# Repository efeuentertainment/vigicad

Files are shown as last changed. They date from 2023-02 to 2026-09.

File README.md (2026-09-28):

Hier entsteht die Bauanleitung zum Botkin 2S, der neuesten Version des Botkin Roboters, basierend auf dem Vigibot Minus 2S

# Minus-Type 2S Robot für Botkins

## Inhalt

<details open>
<summary>[Diesen Abschnitt verbergen]</summary>

* [1. Generelle Info](#1-generelle-info)
* [2. Voraussetzungen](#2-voraussetzungen)
* [3. Teileliste](#3-teileliste)
* [4. Minus Type 2S Zusammenbau](#4-minus-type-2S-zusammenbau)
  * [4.1 Software Installieren](#41-software-installieren)
  * [4.2 Vigibot Online Konfiguration](#42-vigibot-online-konfiguration)
  * [4.3 Zusammenbau Motorplatte](#43-zusammenbau-motorplatte)
  * [4.4 Zusammenbau Body](#44-zusammenbau-body)
  * [4.5 Roboter mit dem WLAN verbinden](#45-roboter-mit-dem-wlan-verbinden)
  * [4.6 Zusammenbau Greifer und Kopf](#46-zusammenbau-greifer-und-kopf)
  * [4.7 Finale Fertigstellung](#47-finale-fertigstellung)
  * [4.8 Optionale Schritte](#48-optionale-schritte)
  * [4.9 Funktionstest](#49-funktionstest)
* [5. Troubleshooting](#5-troubleshooting)
* [6. Credits](#6-credits)

</details>

# 1. Generelle Info
* Dieser Leitfaden behandelt den Botkins 2S, erhältlich als Kit von Botkins oder [robot-maker.com](https://www.robot-maker.com/shop/kits-robots/284-kit-minus-2s-284.html)
* Der Einfachheit halber wird hier nur die Kit-Version beschrieben. Werden Teile selber beschafft, müssen einzelne Teile selber aus den gelisteten Teilen zusammengesucht werden.
* Die Angaben zu rechts oder links in dieser Anleitung sind immer in Fahrtrichtung gesehen.

## 1.1 Das Botkins Charity Project
Erfahre mehr über das Botkins Charity Project:

* Botkins ist ein nichtgewinnorientierter (gemeinnütziger) Verein. Die Arbeit des Vereinsteams geschiecht auf freiwilligenbasis ohne finanzielle Kompensation. Maker:innen können einen Obulus erhalten.
* [botkins.ch](https://botkins.ch)&#x20;
* [Hackaday Page](https://hackaday.io/project/180558-botkins-charity-project)

## 1.2 Vigibot
Erfahre mehr über Vigibot:
Das französische Roboter-Projekt, dessen Software und Hardware Design Botkins benutzt.

* [Robot Maker Post](https://www.robot-maker.com/forum/topic/13010-what-is-vigibot-quest-ce-que-vigibot/)
* [Drive a robot Vigibot.com](https://www.vigibot.com/)

Als Basis dient die Standard Vigibot Minus-Type Version 2S (siehe Bild). Botkins ist zusätlich mit einem LTE/4G Stick ausgerüstet.

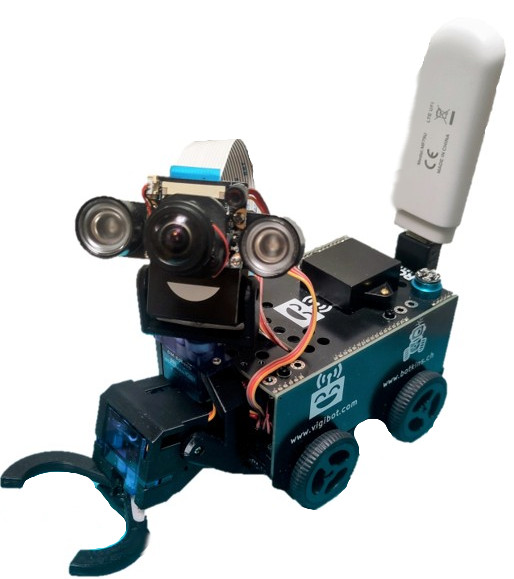
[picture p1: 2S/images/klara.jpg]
Botkins S2


* Wenn du für Botkins einen Roboter bauen möchtest, melde dich bei uns und wir senden dir die nötigen Informationen und den Zugang zu Resourcen.
* Als Maker kannst du die Farbe der 3D-gedruckten Teile selber wählen, sie ist nicht vorgegeben. Kaufst du ein Komplettkit auf robot-maker.com, kannst du dort je nach Verfügbarkeit Teilefarben wählen.
* Der Bau des ersten Roboters kann etwa 5 Stunden dauern, möglicherweise auch länger. Nach etwas Übung dauert der Bau etwa 2 Stunde pro Roboter.
* Bestelle bei uns oder über robot-maker.com das Komplettkit und leg los!

[⬆️ Zurück zum Inhaltsverzeichnis](#inhalt)

# 2. Voraussetzungen

Du benötigst:

* Komplettkit Minus-Type S2 [robot-maker.com](https://www.robot-maker.com/shop/kits-robots/284-kit-minus-2s-284.html) oder bestellbar bei uns an Adresse
* Internetzugang (SIM-Karte mit mobilen Daten, WLAN oder Ethernet-LAN), PC.
* Ein 3D-Drucker ist derzeit nicht erforderlich. Wenn du die 3D-Teile selbst drucken möchtest, werden M2- und M2,5-Schrauben und Muttern, die in der entsprechenden Botkins-Teileliste aufgeführt sind, benötigt. Du findest sie in der Teileliste in jedem der 3D-gedruckten Sektionen.
* Werkzeuge: Schraubenzieher, verstellbarer Schraubenschlüssel/Gabelschlüssel, Pinzette, Klebeband, Sekundenkleber
* SD-Cardreader für microSD

[⬆️ Zurück zum Inhaltsverzeichnis](#inhalt)

# 3. Teileliste

<details close>
<summary>[Diesen Abschnitt anzeigen]</summary>
Zur einfacheren Lesbarkeit schlagen wir eine Bezugsquelle vor und listen Alternativen auf, wo vorhanden. Es ist euch selbstverständlich freigestellt, wo ihr die Teile beschafft.
Die meisten Teile können bei [robot-maker](https://www.robot-maker.com) beschafft werden

## 3.1 Hauptteile

Das Komplettkit gibt es bei [https://www.robot-maker.com](https://www.robot-maker.com/shop/kits-robots/284-kit-minus-2s-284.html) für ca. 360€

| Stk | Benennung | Shop | Alternative\* |
| --- | --- | --- | --- |
| 1 | Raspberry Pi 3B+ (or 3B), 1GB or 2GB | [Link](https://www.robot-maker.com/shop/cartes-programmables/241-raspberry-pi-3b-plus-241.html) | [Alternative](https://www.pi-shop.ch/raspberry-pi-3-model-b/) |
| 1 | Unlocked ZTE MF79 4G / LTE Stick | [Link](https://aliexpress.com/item/1005005844914823.html) | Huawei E3372h (Modell -153, -320 oder -607) |
| 1 | USB - USB 90° adapter | [Link, "Color : Down Angle Black"](https://aliexpress.com/item/1005003690522920.html) | - |
| 1 | USB bracket holder | [Link](https://www.robot-maker.com/shop/impression-3d/261-service-impression-3d-pla-261.html) | - |
| 1 | USB Microphone sind aktuell in Evaluation. Der verlinkte Artikel wird nicht mehr hergestellt. Fragt uns. | [Link](https://www.robot-maker.com/shop/composants/446-microphone-usb-446.html) | [BOYA "Color : BY-M100UA"](https://aliexpress.com/item/1005004133896137.html) |
| 1 | 8-64GB "Endurance" Typ MicroSD Karte | [Link](https://www.robot-maker.com/shop/composants/91-carte-sd-32go-91.html) | [Alternative](https://www.berrybase.ch/sandisk-high-endurance-microsdhc-uhs-i-u3-speicherkarte-adapter-32gb) |
| 1 | Falls keinen vorhanden: CardReader für microSD | [Link](https://www.pi-shop.ch/sandisk-card-reader-usb-3-0-reader) | nach Belieben |
| 1 | Weitwinkelkamera mit Infrarot-Filter | [Link](https://www.robot-maker.com/shop/capteurs/311-camera-raspberry-pi.html) | [Alternative: "Color : Option 10"](https://aliexpress.com/item/1005004276506212.html) |
| 1 | 30cm Verbindungskabel für Kamera (zum ersetzen des kurzen Originals) | [Link](https://www.robot-maker.com/shop/composants/329-nappe-raspberry-pi.html#/92-longueur-30cm) | nach Belieben |
| 1 | Li-Ion Akku 2S | [Link](https://www.robot-maker.com/shop/alimentation/75-batterie-2s-1p-75.html) | - |
| 2 | 6A 67W Fast USB Charger | [Link, "Plug Type: EU Charger only"](https://aliexpress.com/item/1005006632595521.html) | - |
| 1 | USB Kabel magnetisch | [Link, "Color : \*\* type c", "Length : 1m(3.3ft)"](https://www.aliexpress.com/item/4001224959039.html) | [Alternative Kabel](https://www.robot-maker.com/shop/alimentation/608-cable-usb-magnetique-data-608.html) + [Alternative Stecker "USB C"](https://www.robot-maker.com/shop/alimentation/609-embout-magnetique-micro-usb-ou-usb-c-rechargedata-609.html) |
| 1 | USB-A zu USB-C Kabel | [Link, "Color : A-C \*\* ", "Length : 1m"](https://aliexpress.com/item/1005008279278619.html) | nach Belieben |
| 1 | Falls noch keiner Vorhanden: Sekundenkleber | [Link, "1ML x10pcs"](https://aliexpress.com/item/1005008238433750.html) | - |

[⬆️ Zurück zum Inhaltsverzeichnis](#inhalt)
</details>

# 4. Minus Type 2S Zusammenbau

## 4.1 Software Installieren

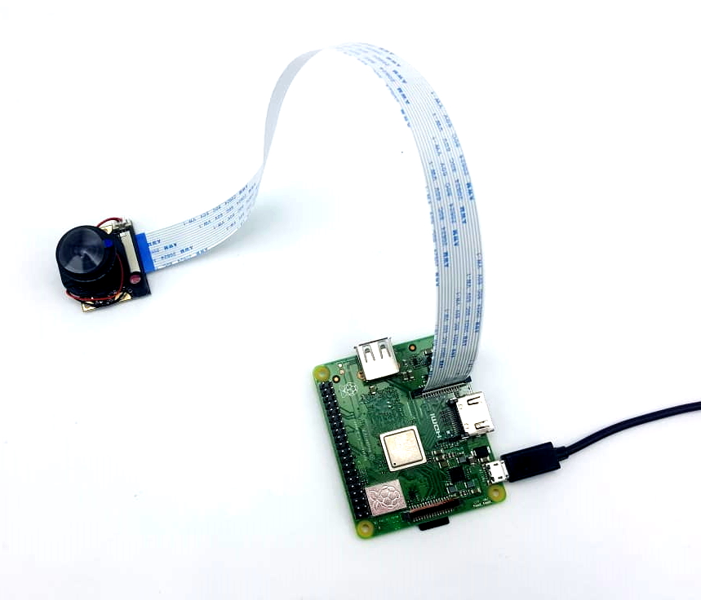
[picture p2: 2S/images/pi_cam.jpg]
pi_cam
<br>

Füge deinen Roboter bei Vigibot ganz einfach hinzu.
Du benötigst: einen Rapsery Pi (empfohlen 3B+), eine 16 oder 32 GB microSD Karte, eine Spannungsversorgung für den Pi, die Kamera mit dem passenden Kabel.
Mit wenigen einfachen Schritten kannst du deine Kamera auf [vigibot.com](https://www.vigibot.com/) live schalten:

* Erstelle auf [vigibot.com](https://www.vigibot.com/) einen Account gemäss den Beschreibungen vom Dokument /Hardware_Design/Overview_Onboarding_Makers.md auf der Botkins Cloud.
* Lade das Image runter: [vigimage.img.zip](https://www.botkins.ch/vigimage.img.zip) und entpacke die ZIP-Datei.
* Um die Image-Datei auf deine microSD Karte schreiben zu können, musst du diese mit dem PC verbinden (Kartenleser) und ein Tool zum Schreiben verwenden. Wir empfehlen den Raspberry Pi Imager oder Balena Etcher. Runterladen, installieren.
* Andere Tools wie das HDD Raw Copy Tool oder win32diskImager gehen auch. ApplePiBacker (Mac).
* Hinweis: Wenn du eine Karte grösser 32GB verwendest, musst du im Pi Imager zuerst das Modell 3 wählen, dann beim Betriebssystem löschen, um die Karte in FAT32 zu formatieren.
* Nach dem Ausführen des Pi Imager musst du das Modell des Pis auswählen, bei uns meist 3B+. Unter Betriebssystem wählst du zuunterst „Eigenes Image auswählen“, suchst das vigimage.img und wählst es aus. Dann wählst du die SD Karte als Zielmedium und bestätigst eine allfällige Überschreibewarnung. Starte den Schreibvorgang. Das dauert nun je nach Schreibgeschwindigkeit der Karte einige Minuten.
* Wenn das gemacht ist, öffne den /boot Ordner deiner SD Card. Windows: Sollte im Explorer der /boot Ordner nicht erscheinen, Drücke Win+R und gibt diskmgmt.msc ein. So gelangst du in die Datenträgerverwaltung. Wenn dort eine 100MB Partition gelistet ist, gib ihr über Rechtsklick > Laufwerkbuchstabe und -pfade ändern einen noch freien Buchstaben.
* Ändere die Datei "robot.json" gemäss dem zuvor gewählten Roboternamen und Roboterpasswort. ( Ändere den „Demo”-Benutzernamen und das „Standard”-Passwort)
* Installiere die SD-Karte im Raspberry Pi mit der installierten Kamera und schalte ihn dann ein (aufgrund des Kompilierungsprozesses dauert der erste Start einige Minuten, bevor der Roboter auf der Website erscheint (bis zu 30 Minuten): Schalte den Raspberry Pi während dieser Zeit nicht aus).

Falls du auf den Pi zugreifen willst:

*	Der Pi und dein PC müssen in gleichen Netzwerk sein. Finde die IP Adresse des Pi raus (Verbindung über deinen Router (häufig hat der Router die IP 192.168.1.1) > Verbundene Geräte oder nutze eine App wie "Fing")
*	Win+R > „Powershell“ > Ausführen öffnet das Terminal
*	Gib im Fenster ein: ssh pi\@IP-ADRESSE (Ersetze die Adresse mit der Adresse des Pi, zB 192.168.1.146)
*	Das Terminal wird dich fragen, ob du sicher bist, eine Verbindung herstellen zu wollen. Schreibe „yes“ und bestätige
*	Standartmässig ist das Passwort „raspberry“.

LTE/4G Mobile Data Stick:

* An einen Windows- oder Mac-PC anschliessen (die Webseite 192.168.8.1 wird geöffnet oder die App auf dem Speichermedium gestartet) und Datenroaming aktivieren.

[⬆️ Zurück zum Inhaltsverzeichnis](#inhalt)

## 4.2 Vigibot Online Konfiguration

### Konfiguration der Fernsteuerung über Vigibot

Klicke auf der Vigibot Seite -> `Management` -> Werkzeug-Symbol (Remote controller configuration) -> `Modifications made` -> Wechsle von `Form` zu `Text` -> ersetze die `{}` mit dem folgenden Code:

<details>
<summary>[SHOW CODE BLOCK]</summary>

```JSON
{
  "BUTTONS": [
    {
      "ICON0": "switch0",
      "ICON1": "switch1",
      "TEXT": "Power Enable",
      "ACTION": "Switch0",
      "SPECIAL": "i0"
    },
    {
      "ICON0": "projecteur0",
      "ICON1": "projecteur1",
      "TEXT": "LED spotlights",
      "ACTION": "Switch1",
      "SPECIAL": "i1"
    },
    {
      "ICON0": "vide",
      "ICON1": "",
      "TEXT": "",
      "ACTION": "",
      "SPECIAL": ""
    },
    {
      "ICON0": "avancer",
      "ICON1": "",
      "TEXT": "Forward",
      "ACTION": "IncrementForward",
      "SPECIAL": "yp"
    },
    {
      "ICON0": "vide",
      "ICON1": "",
      "TEXT": "",
      "ACTION": "",
      "SPECIAL": ""
    },
    {
      "ICON0": "suivant",
      "ICON1": "",
      "TEXT": "Next tool",
      "ACTION": "NextTool",
      "SPECIAL": ""
    },
    {
      "ICON0": "sirene0",
      "ICON1": "sirene1",
      "TEXT": "Buzzer",
      "ACTION": "Switch2",
      "SPECIAL": "i2"
    },
    {
      "ICON0": "lumicont0",
      "ICON1": "lumicont1",
      "TEXT": "Maximize the brightness and contrast",
      "ACTION": "Switch3",
      "SPECIAL": "i3"
    },
    {
      "ICON0": "gauche",
      "ICON1": "",
      "TEXT": "Left",
      "ACTION": "IncrementTurnLeft",
      "SPECIAL": "zn"
    },
    {
      "ICON0": "stopper",
      "ICON1": "",
      "TEXT": "Click to stop or drag to drive",
      "ACTION": "Brake",
      "SPECIAL": "st"
    },
    {
      "ICON0": "droite",
      "ICON1": "",
      "TEXT": "Right",
      "ACTION": "IncrementTurnRight",
      "SPECIAL": "zp"
    },
    {
      "ICON0": "centrer",
      "ICON1": "",
      "TEXT": "Reset tools",
      "ACTION": "ResetTools",
      "SPECIAL": ""
    },
    {
      "ICON0": "gyrophare0",
      "ICON1": "gyrophare1",
      "TEXT": "Warning light mode",
      "ACTION": "Switch4",
      "SPECIAL": "i4"
    },
    {
      "ICON0": "vide",
      "ICON1": "",
      "TEXT": "",
      "ACTION": "",
      "SPECIAL": ""
    },
    {
      "ICON0": "vide",
      "ICON1": "",
      "TEXT": "",
      "ACTION": "",
      "SPECIAL": ""
    },
    {
      "ICON0": "reculer",
      "ICON1": "",
      "TEXT": "Backward",
      "ACTION": "IncrementBackward",
      "SPECIAL": "yn"
    },
    {
      "ICON0": "capture",
      "ICON1": "",
      "TEXT": "Capture the last seconds of video",
      "ACTION": "",
      "SPECIAL": "capture"
    },
    {
      "ICON0": "precedent",
      "ICON1": "",
      "TEXT": "Previous tool",
      "ACTION": "PreviousTool",
      "SPECIAL": ""
    },
    {
      "ICON0": "vide",
      "ICON1": "",
      "TEXT": "",
      "ACTION": "",
      "SPECIAL": ""
    },
    {
      "ICON0": "vide",
      "ICON1": "",
      "TEXT": "",
      "ACTION": "",
      "SPECIAL": ""
    },
    {
      "ICON0": "lock0",
      "ICON1": "lock1",
      "TEXT": "Unlink remote control and video",
      "ACTION": "",
      "SPECIAL": "switchlock"
    },
    {
      "ICON0": "osd0",
      "ICON1": "osd1",
      "TEXT": "Toggle OSD",
      "ACTION": "",
      "SPECIAL": "switchosd"
    },
    {
      "ICON0": "vide",
      "ICON1": "",
      "TEXT": "",
      "ACTION": "",
      "SPECIAL": ""
    },
    {
      "ICON0": "dodo",
      "ICON1": "",
      "TEXT": "Put on standby",
      "ACTION": "Sleep",
      "SPECIAL": ""
    },
    {
      "ICON0": "vide",
      "ICON1": "",
      "TEXT": "",
      "ACTION": "",
      "SPECIAL": ""
    },
    {
      "ICON0": "vide",
      "ICON1": "",
      "TEXT": "",
      "ACTION": "",
      "SPECIAL": ""
    },
    {
      "ICON0": "vide",
      "ICON1": "",
      "TEXT": "",
      "ACTION": "",
      "SPECIAL": ""
    },
    {
      "ICON0": "exit",
      "ICON1": "",
      "TEXT": "Restart the client process",
      "ACTION": "ExitRobot",
      "SPECIAL": "confirm"
    },
    {
      "ICON0": "reboot",
      "ICON1": "",
      "TEXT": "Reboot the system",
      "ACTION": "RebootRobot",
      "SPECIAL": "confirm"
    },
    {
      "ICON0": "poweroff",
      "ICON1": "",
      "TEXT": "Power off the system",
      "ACTION": "PowerOffRobot",
      "SPECIAL": "confirm"
    }
  ],
  "COMMANDS": [
    {
      "NAME": "Turret control",
      "CAMERA": 0,
      "MIXING": 0,
      "GAINX": 80,
      "GAINY": 80
    },
    {
      "NAME": "Gripper control",
      "CAMERA": 0,
      "MIXING": 1,
      "GAINX": 80,
      "GAINY": 80
    },
    {
      "NAME": "250 Kbps - Camera control",
      "CAMERA": 1,
      "MIXING": 0,
      "GAINX": 80,
      "GAINY": 80
    },
    {
      "NAME": "250 Kbps - Gripper control",
      "CAMERA": 1,
      "MIXING": 1,
      "GAINX": 80,
      "GAINY": 80
    }
  ],
  "TX": {
    "COMMANDS16": [
      {
        "NAME": "Turret X",
        "INIT": 0,
        "SCALEMIN": -180,
        "SCALEMAX": 180,
        "MIN": -90,
        "MAX": 90,
        "CLAMPMIN": -20,
        "CLAMPMAX": 20,
        "SIGNED": true,
        "NBDIGITS": 2,
        "UNIT": "°"
      },
      {
        "NAME": "Turret Y",
        "INIT": 8,
        "SCALEMIN": -180,
        "SCALEMAX": 180,
        "MIN": -55,
        "MAX": 55,
        "CLAMPMIN": -40,
        "CLAMPMAX": 20,
        "SIGNED": true,
        "NBDIGITS": 2,
        "UNIT": "°"
      },
      {
        "NAME": "Gripper X",
        "INIT": 0,
        "SCALEMIN": -180,
        "SCALEMAX": 180,
        "MIN": -35,
        "MAX": 70,
        "CLAMPMIN": -35,
        "CLAMPMAX": 65,
        "SIGNED": true,
        "NBDIGITS": 2,
        "UNIT": "°"
      },
      {
        "NAME": "Gripper Y",
        "INIT": 20,
        "SCALEMIN": -180,
        "SCALEMAX": 180,
        "MIN": -40,
        "MAX": 80,
        "CLAMPMIN": 0,
        "CLAMPMAX": 45,
        "SIGNED": true,
        "NBDIGITS": 2,
        "UNIT": "°"
      }
    ],
    "COMMANDS1": [
      {
        "NAME": "Power Enable",
        "INIT": 1
      },
      {
        "NAME": "LED spotlights",
        "INIT": 1
      },
      {
        "NAME": "Buzzer",
        "INIT": 0
      },
      {
        "NAME": "Brightness boost",
        "INIT": 0
      },
      {
        "NAME": "Switch 4",
        "INIT": 0
      },
      {
        "NAME": "Switch 5",
        "INIT": 0
      },
      {
        "NAME": "Switch 6",
        "INIT": 0
      },
      {
        "NAME": "Switch 7",
        "INIT": 0
      }
    ]
  },
  "RX": {
    "VALUES16": [
      {
        "NAME": "Voltage",
        "INIT": 3,
        "SCALEMIN": 6,
        "SCALEMAX": 9,
        "MIN": 6,
        "MAX": 9,
        "SIGNED": false,
        "NBDIGITS": 2,
        "UNIT": " V"
      },
      {
        "NAME": "Current",
        "INIT": 0,
        "SCALEMIN": -5,
        "SCALEMAX": 5,
        "MIN": -5,
        "MAX": 5,
        "SIGNED": true,
        "NBDIGITS": 2,
        "UNIT": " A"
      }
    ]
  }
}
```

</details>

### Hardware Konfiguration

Klicke auf der Vigibot Seite -> `Management` -> Zahnradsymbol (Hardware configuration) -> `Modifications made` -> Wechsle von `Form` zu `Text` -> ersetze `{}` mit dem folgenden Code:

<details>
<summary>[SHOW CODE BLOCK]</summary>

*Sicherstellen, dass es die  2S Config ist!*

```JSON
{
  "CAMERAS": [
    {
      "TYPE": "",
      "SOURCE": 0,
      "WIDTH": 640,
      "HEIGHT": 480,
      "FPS": 30,
      "BITRATE": 1500000,
      "ROTATE": 180,
      "BRIGHTNESS": 50,
      "CONTRAST": -5,
      "BRIGHTNESSBOOST": 80,
      "CONTRASTBOOST": 100
    },
    {
      "TYPE": "",
      "SOURCE": 0,
      "WIDTH": 640,
      "HEIGHT": 480,
      "FPS": 30,
      "BITRATE": 250000,
      "ROTATE": 180,
      "BRIGHTNESS": 50,
      "CONTRAST": -5,
      "BRIGHTNESSBOOST": 80,
      "CONTRASTBOOST": 100
    }
  ],
  "OUTPUTS": [
    {
      "NAME": "Turret pan",
      "TYPE": "Servos",
      "ADRESSE": -1,
      "GPIOS": [
        5
      ],
      "SLEEPMODES": [
        "Floating"
      ],
      "INS": [
        -135,
        135
      ],
      "OUTS": [
        500,
        2400
      ],
      "BACKSLASH": 0,
      "COMMANDS16": [
        0
      ],
      "GAINS16": [
        -1
      ],
      "COMMANDS8": [],
      "GAINS8": [],
      "COMMANDS1": [],
      "GAINS1": []
    },
    {
      "NAME": "Turret tilt",
      "TYPE": "Servos",
      "ADRESSE": -1,
      "GPIOS": [
        6
      ],
      "SLEEPMODES": [
        "Floating"
      ],
      "INS": [
        -90,
        90
      ],
      "OUTS": [
        500,
        2500
      ],
      "BACKSLASH": 0,
      "COMMANDS16": [
        1
      ],
      "GAINS16": [
        -1
      ],
      "COMMANDS8": [],
      "GAINS8": [],
      "COMMANDS1": [],
      "GAINS1": []
    },
    {
      "NAME": "Gripper claw",
      "TYPE": "Servos",
      "ADRESSE": -1,
      "GPIOS": [
        7
      ],
      "SLEEPMODES": [
        "Floating"
      ],
      "INS": [
        -90,
        90
      ],
      "OUTS": [
        500,
        2500
      ],
      "BACKSLASH": 0,
      "COMMANDS16": [
        2
      ],
      "GAINS16": [
        -1
      ],
      "COMMANDS8": [],
      "GAINS8": [],
      "COMMANDS1": [],
      "GAINS1": []
    },
    {
      "NAME": "Gripper tilt",
      "TYPE": "Servos",
      "ADRESSE": -1,
      "GPIOS": [
        8
      ],
      "SLEEPMODES": [
        "Floating"
      ],
      "INS": [
        -90,
        90
      ],
      "OUTS": [
        500,
        2500
      ],
      "BACKSLASH": 0,
      "COMMANDS16": [
        3
      ],
      "GAINS16": [
        -1
      ],
      "COMMANDS8": [],
      "GAINS8": [],
      "COMMANDS1": [],
      "GAINS1": []
    },
    {
      "NAME": "Front left wheel",
      "TYPE": "PwmPwm",
      "ADRESSE": -1,
      "GPIOS": [
        22,
        23
      ],
      "SLEEPMODES": [
        "Low",
        "Low"
      ],
      "INS": [
        -100,
        -1,
        1,
        100
      ],
      "OUTS": [
        -100,
        -1,
        1,
        100
      ],
      "BACKSLASH": 0,
      "COMMANDS16": [],
      "GAINS16": [],
      "COMMANDS8": [
        0,
        1,
        2
      ],
      "GAINS8": [
        1,
        1,
        -1
      ],
      "COMMANDS1": [],
      "GAINS1": []
    },
    {
      "NAME": "Front right wheel",
      "TYPE": "PwmPwm",
      "ADRESSE": -1,
      "GPIOS": [
        24,
        25
      ],
      "SLEEPMODES": [
        "Low",
        "Low"
      ],
      "INS": [
        -100,
        -1,
        1,
        100
      ],
      "OUTS": [
        -100,
        -1,
        1,
        100
      ],
      "BACKSLASH": 0,
      "COMMANDS16": [],
      "GAINS16": [],
      "COMMANDS8": [
        0,
        1,
        2
      ],
      "GAINS8": [
        1,
        -1,
        -1
      ],
      "COMMANDS1": [],
      "GAINS1": []
    },
    {
      "NAME": "Rear left wheel",
      "TYPE": "PwmPwm",
      "ADRESSE": -1,
      "GPIOS": [
        16,
        17
      ],
      "SLEEPMODES": [
        "Low",
        "Low"
      ],
      "INS": [
        -100,
        -1,
        1,
        100
      ],
      "OUTS": [
        -100,
        -1,
        1,
        100
      ],
      "BACKSLASH": 0,
      "COMMANDS16": [],
      "GAINS16": [],
      "COMMANDS8": [
        0,
        1,
        2
      ],
      "GAINS8": [
        -1,
        1,
        -1
      ],
      "COMMANDS1": [],
      "GAINS1": []
    },
    {
      "NAME": "Rear right wheel",
      "TYPE": "PwmPwm",
      "ADRESSE": -1,
      "GPIOS": [
        26,
        27
      ],
      "SLEEPMODES": [
        "Low",
        "Low"
      ],
      "INS": [
        -100,
        -1,
        1,
        100
      ],
      "OUTS": [
        -100,
        -1,
        1,
        100
      ],
      "BACKSLASH": 0,
      "COMMANDS16": [],
      "GAINS16": [],
      "COMMANDS8": [
        0,
        1,
        2
      ],
      "GAINS8": [
        -1,
        -1,
        -1
      ],
      "COMMANDS1": [],
      "GAINS1": []
    },
    {
      "NAME": "Power Enable",
      "TYPE": "Gpios",
      "ADRESSE": -1,
      "GPIOS": [
        13
      ],
      "SLEEPMODES": [
        "Low"
      ],
      "INS": [
        0,
        1
      ],
      "OUTS": [
        0,
        1
      ],
      "BACKSLASH": 0,
      "COMMANDS16": [],
      "GAINS16": [],
      "COMMANDS8": [],
      "GAINS8": [],
      "COMMANDS1": [
        0
      ],
      "GAINS1": [
        1
      ]
    },
    {
      "NAME": "LED spotlights",
      "TYPE": "Gpios",
      "ADRESSE": -1,
      "GPIOS": [
        9
      ],
      "SLEEPMODES": [
        "Low"
      ],
      "INS": [
        0,
        1
      ],
      "OUTS": [
        0,
        1
      ],
      "BACKSLASH": 0,
      "COMMANDS16": [],
      "GAINS16": [],
      "COMMANDS8": [],
      "GAINS8": [],
      "COMMANDS1": [
        1
      ],
      "GAINS1": [
        1
      ]
    },
    {
      "NAME": "Buzzer",
      "TYPE": "Pwms",
      "ADRESSE": -1,
      "GPIOS": [
        4
      ],
      "SLEEPMODES": [
        "None"
      ],
      "INS": [
        0,
        1
      ],
      "OUTS": [
        0,
        80
      ],
      "BACKSLASH": 0,
      "COMMANDS16": [],
      "GAINS16": [],
      "COMMANDS8": [],
      "GAINS8": [],
      "COMMANDS1": [
        2
      ],
      "GAINS1": [
        1
      ]
    },
    {
      "NAME": "Maximize the brightness and contrast",
      "TYPE": "Gpios",
      "ADRESSE": -1,
      "GPIOS": [
        1
      ],
      "SLEEPMODES": [
        "None"
      ],
      "INS": [
        0,
        1
      ],
      "OUTS": [
        0,
        1
      ],
      "BACKSLASH": 0,
      "COMMANDS16": [],
      "GAINS16": [],
      "COMMANDS8": [],
      "GAINS8": [],
      "COMMANDS1": [
        3
      ],
      "GAINS1": [
        1
      ]
    },
    {
      "NAME": "Switch 4",
      "TYPE": "Servos",
      "ADRESSE": -1,
      "GPIOS": [
        18
      ],
      "SLEEPMODES": [
        "None"
      ],
      "INS": [
        0,
        1
      ],
      "OUTS": [
        1000,
        2000
      ],
      "BACKSLASH": 0,
      "COMMANDS16": [],
      "GAINS16": [],
      "COMMANDS8": [],
      "GAINS8": [],
      "COMMANDS1": [
        4
      ],
      "GAINS1": [
        1
      ]
    },
    {
      "NAME": "Switch 5",
      "TYPE": "Gpios",
      "ADRESSE": -1,
      "GPIOS": [
        19
      ],
      "SLEEPMODES": [
        "None"
      ],
      "INS": [
        0,
        1
      ],
      "OUTS": [
        0,
        1
      ],
      "BACKSLASH": 0,
      "COMMANDS16": [],
      "GAINS16": [],
      "COMMANDS8": [],
      "GAINS8": [],
      "COMMANDS1": [
        5
      ],
      "GAINS1": [
        1
      ]
    },
    {
      "NAME": "Switch 6",
      "TYPE": "Gpios",
      "ADRESSE": -1,
      "GPIOS": [
        20
      ],
      "SLEEPMODES": [
        "None"
      ],
      "INS": [
        0,
        1
      ],
      "OUTS": [
        0,
        1
      ],
      "BACKSLASH": 0,
      "COMMANDS16": [],
      "GAINS16": [],
      "COMMANDS8": [],
      "GAINS8": [],
      "COMMANDS1": [
        6
      ],
      "GAINS1": [
        1
      ]
    },
    {
      "NAME": "Switch 7",
      "TYPE": "Gpios",
      "ADRESSE": -1,
      "GPIOS": [
        21
      ],
      "SLEEPMODES": [
        "None"
      ],
      "INS": [
        0,
        1
      ],
      "OUTS": [
        0,
        1
      ],
      "BACKSLASH": 0,
      "COMMANDS16": [],
      "GAINS16": [],
      "COMMANDS8": [],
      "GAINS8": [],
      "COMMANDS1": [
        7
      ],
      "GAINS1": [
        1
      ]
    }
  ],
  "COMMANDS8": [
    {
      "RAMPUP": 0,
      "RAMPDOWN": 0,
      "RAMPINIT": 0,
      "FAILSAFE": true,
      "SLEEP": true
    },
    {
      "RAMPUP": 15,
      "RAMPDOWN": 15,
      "RAMPINIT": 15,
      "FAILSAFE": true,
      "SLEEP": true
    },
    {
      "RAMPUP": 15,
      "RAMPDOWN": 15,
      "RAMPINIT": 15,
      "FAILSAFE": true,
      "SLEEP": true
    }
  ],
  "PWMFREQUENCY": 1000
}
```
[⬆️ Zurück zum Inhaltsverzeichnis](#inhalt)
</details>

## 4.3 Zusammenbau Motorplatte

Benötigtes Material aus dem Kit:

| Stk | Benennung | Teilenummer (*tbc) |
| --- | --- | --- |
| 1 | 3D gedruckte Basis | *Druckteile/Chassis/2S101.0 Basis.step | 
| 1 | 3D gedruckter Batteriehalter | *Druckteile/Chassis/2S102.0 Batteriehalter.step |
| 1 | 3D gedruckter Halter für Greifer und Kopf | *Druckteile/Chassis/2S103.0 Kopf und Greiferhalter.step|
| 1 | Basisprint | aus Kit |
| 4 | Pololu 100:1 Getriebemotoren HP 6V <br> mit Federkontakten| aus Kit | 
| 3 | Schrauben für Befestigung Halter | *tbd* |
| 2 | Schrauben für Befestigung  Basisprint | Kreuzschlitzschraube M2x5 |
| 2 | Schrauben für Befestigung  Basisprint inkl. Batteriehalter| Kreuzschlitzschraube M2x8 |
| 4 | Räder 32mm (Bohrung Motorwelle Ø3mm, max.Ø 50mm) | [Link](https://www.robot-maker.com/shop/elements-mecaniques/171-roue-32mm-171.html?) | 
| 1 | Batterie 2S | aus Kit | 

Hinweis: Die Bilder zeigen In-6kt Schrauben für die Befestigung des Halter Greifer und Kopf. Das dürfen natürlich auch Kreuzschlitzschrauben sein.

Einlegen der vier Motoren in die Vertiefungen in der Basis, Pins gegen oben

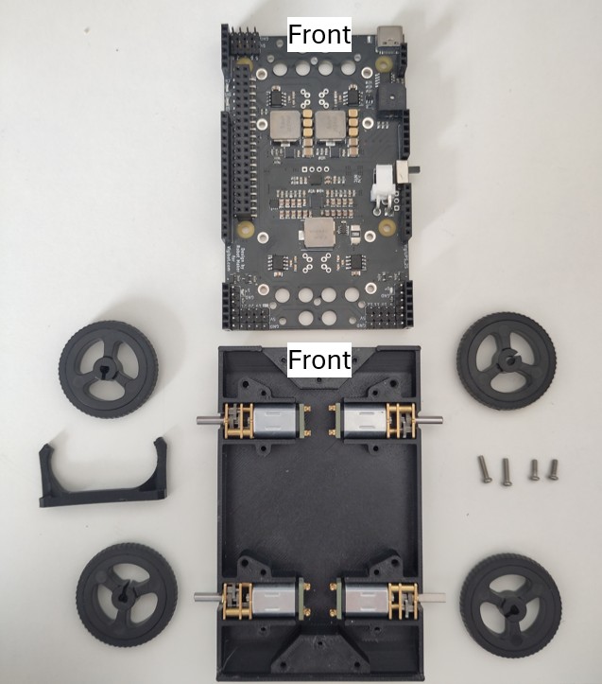
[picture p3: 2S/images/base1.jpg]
 <br>

Halter Greifer und Kopf in Aussparung einlegen, Basisprint auflegen.
Halter Greifer und Kopf mit drei Schrauben befestigen, Batteriehalter Basisprint mit 2x  M2x8 Schrauben befestigen, Basisprint mit zwei weiteren M2x5 befestigen. Zusätzlich kann hinten noch eine Schraube M2x5 verbaut werden (siehe Bild).

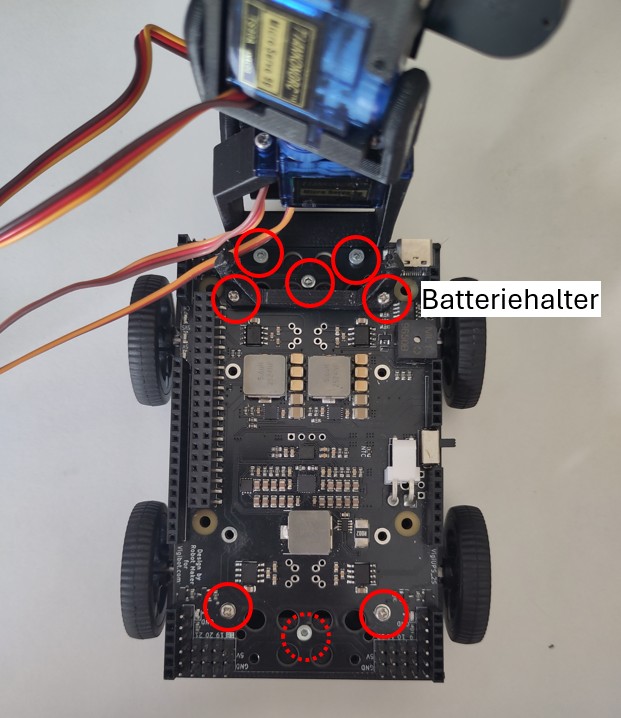
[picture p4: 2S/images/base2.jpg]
 <br>

Die Räder können aufgesteckt, der Akku eingesteckt und im Batteriehalter platziert werden.

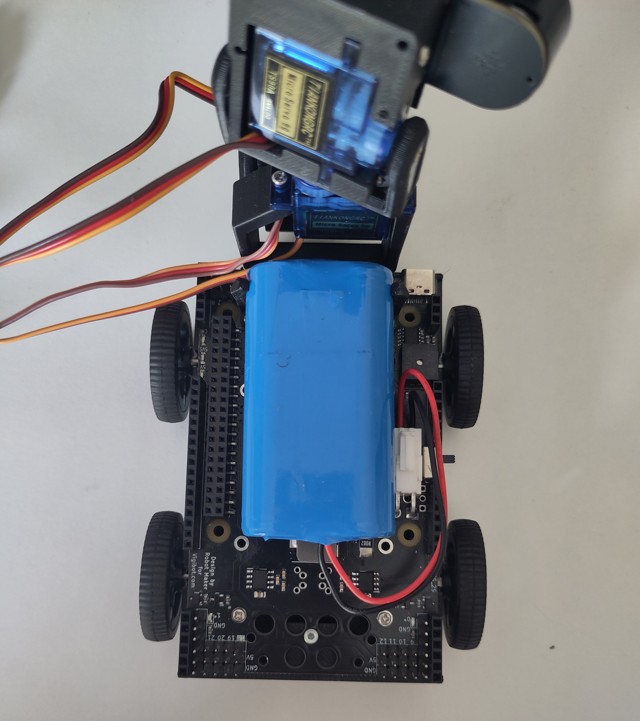
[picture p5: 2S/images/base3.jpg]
 <br>

Servokabel des Kopfes gem. folgenden Abbildungen mit dem Basisprint verbinden. Die Abbildungen sind ohne Greifer und Kopf dargestellt.

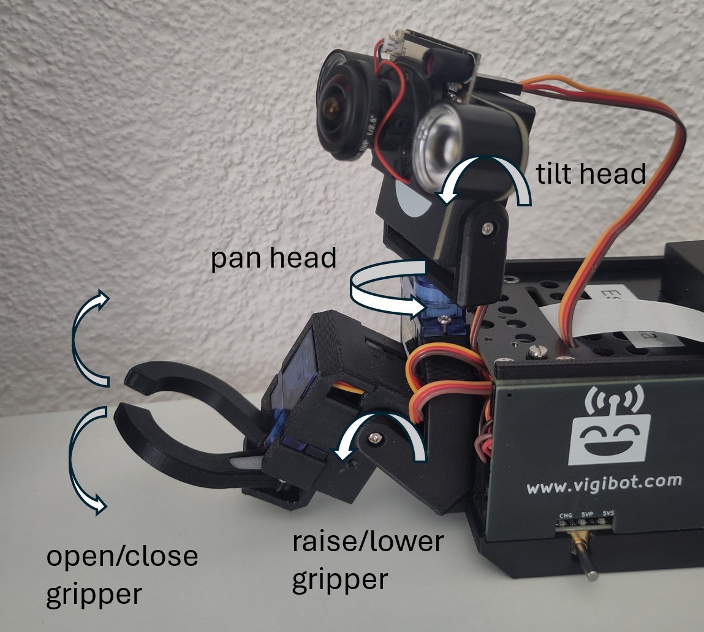
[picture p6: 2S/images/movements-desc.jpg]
Bewegungen Kopf und Greifer
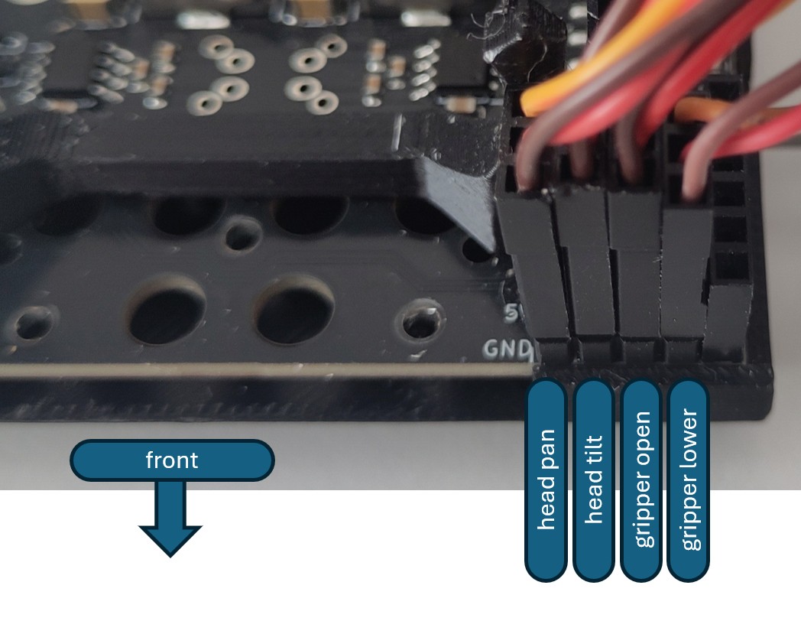
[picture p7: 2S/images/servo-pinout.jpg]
Steckerbelegung
 <br>

[⬆️ Zurück zum Inhaltsverzeichnis](#inhalt)

## 4.4 Zusammenbau Body

Benötigtes Material aus dem Kit:

| Stk | Benennung | Teilenummer |
| --- | --- | --- |
| 1 | Seitenplatte links | Seite mit Aufdruck botkins.ch | 
| 1 | Seitenplatte rechts | Seite mit Aufdruck On/Off |
| 1 | Rapsberry Pi 3B+ | aus Kit |
| 1 | microSD ca. 16GB inkl. Programm drauf | aus Kit, Programmbeschreibung oben |
| 1 | Verbinderleiste | aus Kit |
| 1 | Deckprint | aus Kit | 
| 4 | Schrauben für Befestigung Pi | M2.5x6 |
| 4 | Distanzbolzen für Befestigung Pi | M2.5x5 M-F |
| 4 | Muttern für Befestigung Pi | M2.5 |
| 1 | Flachbandkabel Pi <> Kamera | 30cm |
| 1 | Lautsprecher | aus Kit | 
| 2 | Schrauben zur Befestigung des Lautsprechers | M2x6 |
| 2 | Distanzbolzen zur Befestigung des Lautsprechers | M2x5 M-F |
| 2 | Muttern zur Befestigung des Lautsprechers | M2 |
| 1 | Verbindungskabel Deckprint zur Kamera | Servokabel F-F 20cm |
| 1 | Mikrophon | aus Kit |
| 1 | gedruckte Pinabdeckung und Auffahrschutz 4G Stick | *tbd* |
| 1*  | 4G/LTE Stick | *tbd* |
| 1 | 90° USB Winkelstecker für 4G/LTE Stick | *tbd* |
| 1 | Drehlicht | aus Kit | 

*Optinale Teile

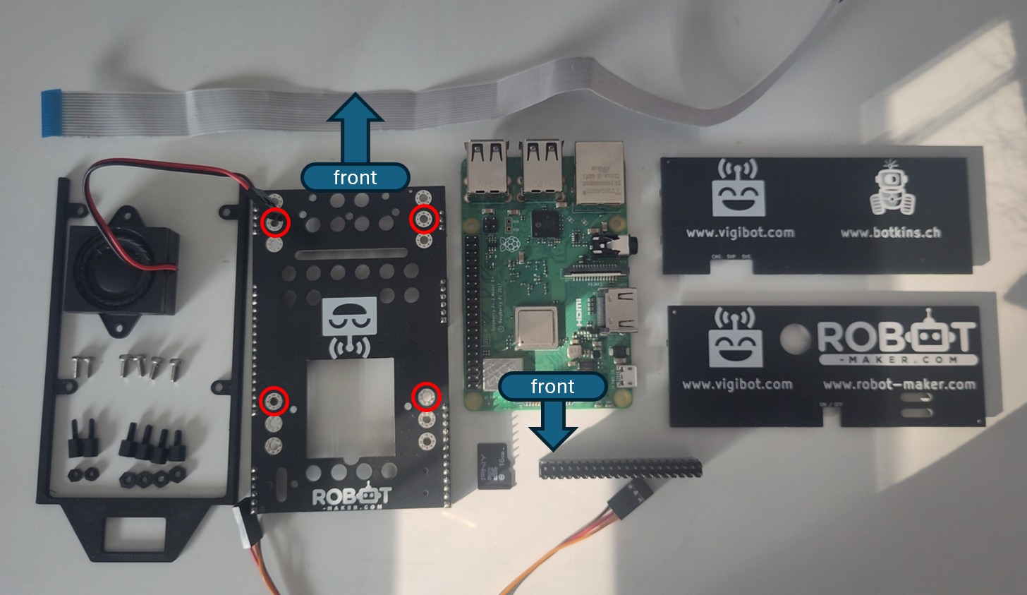
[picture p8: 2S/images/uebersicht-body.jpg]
body complete


Hinweis: Das Drehlicht fehlt auf dem Bild

Distanzbolzen für Lautsprecher montieren: M2x5 M-F Distanzbolzen von oben durch die Löcher stecken, von unten mit Mutter sichern. Kabel durch Ausschnitt stecken, Lautsprecher mit Membran nach unten (Schutz) montieren. Lautsprecherkabel mit dem Print verbinden, auf Polarität achten. Rot ist +, Schwarz-.

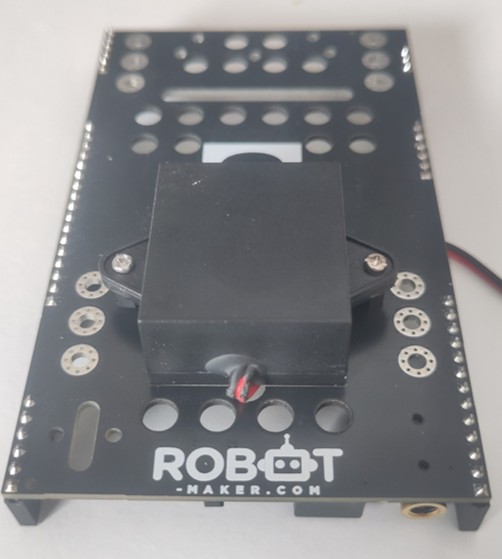
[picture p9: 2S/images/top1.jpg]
Speaker Assembly Top
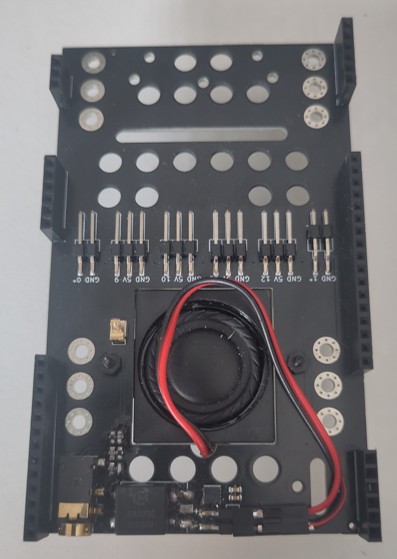
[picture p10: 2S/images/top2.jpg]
Speaker Assembly Bottom
 

Pi am Deckprint befestigen:
Die im Übersichtsbild rot eingekreisten Löcher verwenden, Distanzbolzen M2.5x5 M-F von unten durchstecken, oben die gedruckte Pinabdeckung auflegen und beides mit einer Mutter M2.5 sichern.

Pin Cover Top Print

Servoverlängerungskabel (Spannungsversorgung Kameraprint) auf der Unterseite des Deckpins in Anschluss 12 einstecken. Gelb ist das Signalkabel, Rot + und Braun GND.

Camera Cable

Flachbandkabel für die Kamera am Pi befestigen. Dazu den schwarzen Klemmbalken bei der Kamerabuchse (siehe Beschriftung auf dem Pi) nach oben ziehen, um Buchse zu "öffnen". Von oben in Buchse schauen und Kabel so reinstecken, dass die Kontakte des Kabels zu den Kontakten der Buchse zeigen.
Klemmbalken reindrücken, durch leichten Zug am Flachbandkabel korrekten Sitz prüfen.

Die microSD Card in den Karten-Slot auf der vorderen kurzen Seite des Pi einstecken.

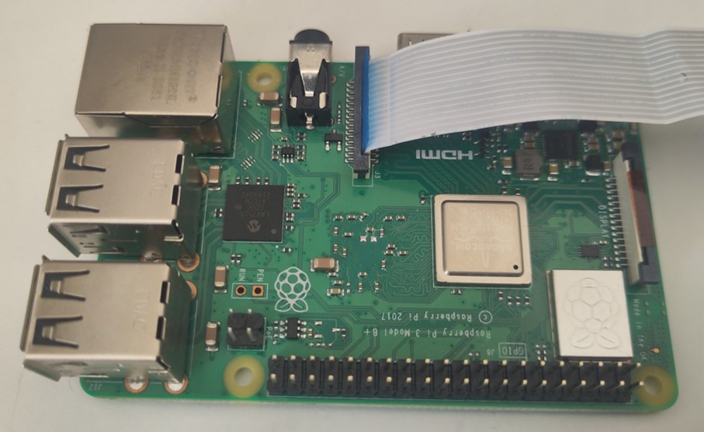
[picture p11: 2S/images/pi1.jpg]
Camera Signal Cable


Den Deckprint mit der Unterseite gegen oben auf den Tisch legen, das Flachbandkabel der Kamera unter dem Pi durch den Schlitz im Deckprint führen. Den Pi mit den Anschlüssen gegen hinten auf den Deckprint legen. 90° USB Adapter in USB-Anschluss Mitte-Unten (auf dem Tisch Mitte-Oben) einstecken. Befestigungslöcher des Pi mit den Gewinden in den Distanzbolzen in Deckung bringen und mit den M2.5x6 Schrauben befestigen. Dazu muss evtl. der USB-Adapter ein wenig aus der USB Buchse gezogen werden. Der Adapter sollte im Druckteil eingepasst sein.

Pi Assembly

Verbinderleiste auf die Stiftleister des Pi stecken

Alle vier Servos, die für Greifer und Kopf verbaut werden, in den Baseprint einstecken. Wir bauen den ganzen Body zusammen, damit wir ihn einschalten und die Servos zentrieren können, bevor wir den Greifer und Kopf zusammenbauen. So wird die Montage einfacher.

Unterbau mit Rädern und Akku zur Hand nehmen. Seitenplatten rechts (mit On/Off Aufdruck) und links (mit botkins.ch Aufdruck) auf den Base-Print stecken. 

Die ganze Deckprint-Baugruppe mit dem Pi auf die Seitenwände aufstecken. Nun wirds knifflig: Die seitlichen Pins müssen in die Leisten des Deckprints und gleichzeitig müssen die Pins der Verbindungsleiste vom Pi auf den Baseprint korrekt platziert werden. Dazu von hinten in den Robo schauen und durch seitliches Drücken die Stifte in die Leiste führen. Alles soweit zusammenstecken, dass der Deckprint und die Seitenplatten bündig zusammengefügt sind.

Kompletter Body

Mikrofon an einem der USB Anschlüsse einstecken

Nun kann der Roboter zum ersten Mal eingeschaltet werden! Es dauert etwa 30s, dann stellen sich die Servos in die Mittelposition. Theoretische kannst du den Robo mit BotikinsAP mit einem WLAN verbinden und schon rumfahren :-)

## 4.5 Roboter mit dem WLAN verbinden

Verbindest du den Roboter zum ersten Mal mit einem WLAN, muss er dessen Passwort kennen. Bei den Botkins-Sets haben wir ein Programm vorinstalliert, dass dir das Verbinden vereinfacht. Vorgehen:
* Roboter einschalten
* 30s warten
* Auf einem Smartphone oder Tablet die verfügbaren WLAN suchen und nach `BotkinsAP` suchen. Das Passwort lautet `03Sessel`.
* Nun kannst du dich anmelden, wenn du den Browser öffnest, sollte eine Seite öffnen, in der du die verfügbaren WLAN auswählen und das Passwort des gewünschten WLANS eingeben kannst.
* Hast du das erledigt, werden diese Zugangsdaten im Roboter gespeichert und stehen beim nächsten Mal im gleichen Netz wieder zur Verfügung. Das funktioniert auch mit einem Hotspot eines anderen Smartphones.

Balena Startseite

Nun kannst du dich auf Vigibot mit dem Account des Roboters einloggen und herumfahren.

Hier die Erklärung der Standardbedienelemente:

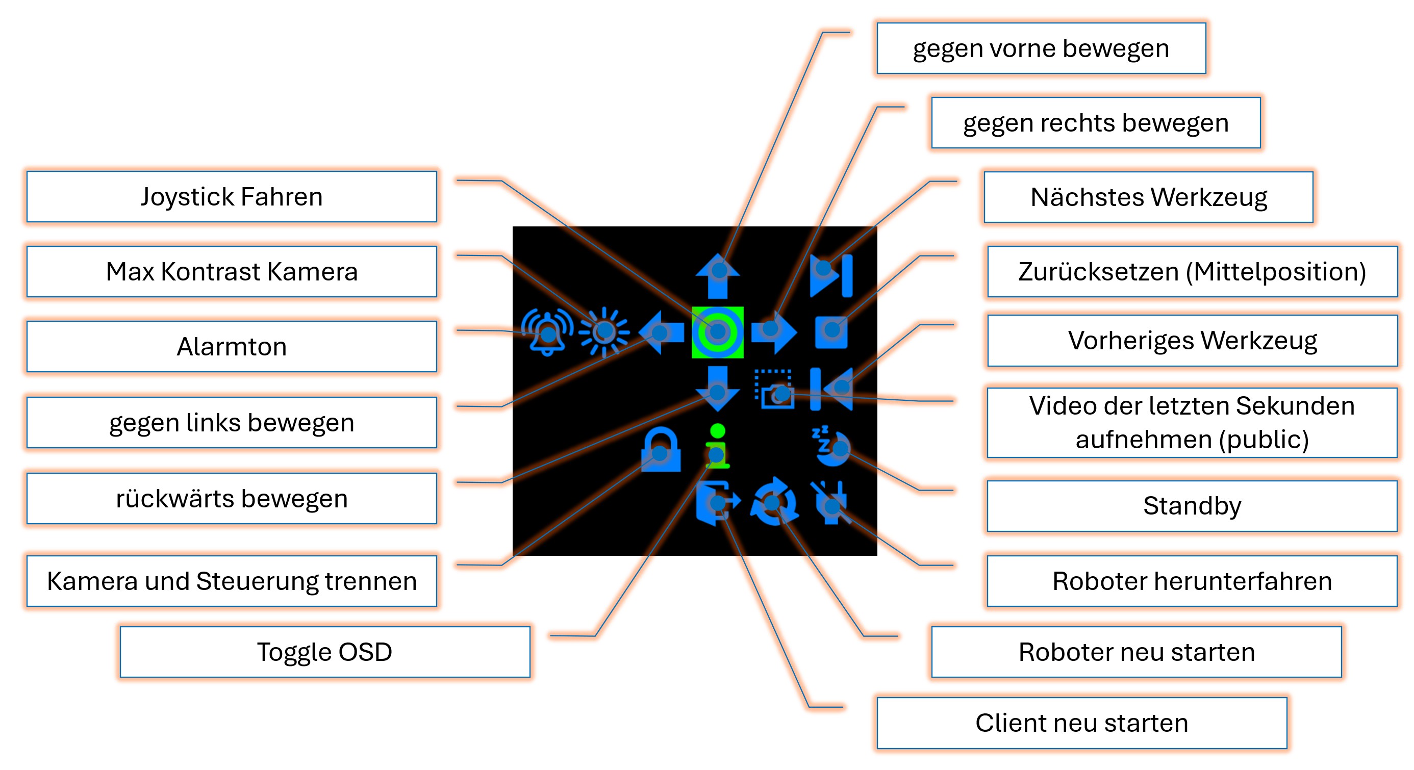
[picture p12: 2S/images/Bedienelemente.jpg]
Vigibot Bedienelemente


[⬆️ Zurück zum Inhaltsverzeichnis](#inhalt)

## 4.6 Zusammenbau Greifer und Kopf

Zuerst wird die Greifer und Kopf Baugruppe zusammengesetzt. Diese wird dann in die Basis eingebaut. Danach wird der Body fertiggestellt.

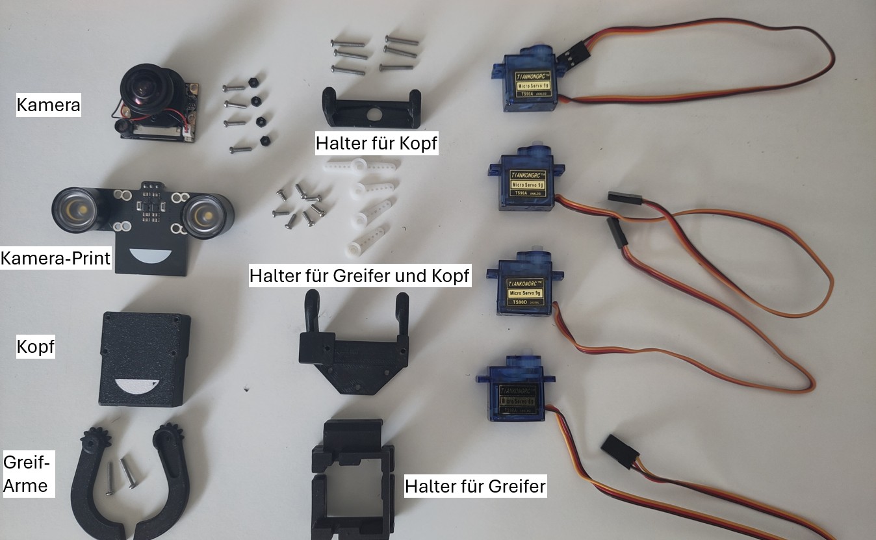
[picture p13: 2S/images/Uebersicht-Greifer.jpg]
Übersicht Greiferteile


Benötigtes Material aus dem Kit:

| Stk | Benennung | Teilenummer (*tbc) |
| --- | --- | --- |
| 1 | 3D gedruckter Kopf | *Druckteile/... | 
| 1 | 3D gedruckter Halter für Kopf | *Druckteile/... |
| 1 | 3D gedruckter Halter für Greifer und Kopf | *Druckteile/... |
| 1 | 3D gedruckter Halter für Greifer | *Druckteile/... |
| 1 | 3D gedruckter Greifarm rechts | *Druckteile/... |
| 1 | 3D gedruckter Greifarm links | *Druckteile/... |
| 1 | Kamera | aus Kit |
| 1 | Kamera-Print mit IR LEDS | aus Kit |
| 3 | Servohörner einseitig | aus Zubehör Servos |
| 1 | Servohorn zwei seitig | aus Zubehör Servos |
| 4 | Servos | 9g |
| 4 | Schrauben für Befestigung  Kamera an Kopf | Kreuzschlitzschraube M2x8 |
| 4 | 6kt-Mutter Kunststoff für Befestigung  Kamera an Kopf | M2 |
| 6 | Schrauben für Befestigung  Servos an Druckteilen | Kreuzschlitzschraube M2x14 |
| 2 | Schrauben für Befestigung Servo Kopfschütteln an Halter | Kreuzschlitzschraube M2x5 |
| 2 | Schrauben für Befestigung Greifarme am Halter für Greifer| Kreuzschlitzschraube M2x12 |
| 2 | Schrauben für Befestigung Servo Greifer an Halter | Kreuzschlitzschraube M2x5 |

Hinweis zu den Schrauben: Wir schlagen Kreuzschlitzschrauben vor, weil deren Kopfhöhe kleiner ist als bei anderen Antrieben. Aber andere Schrauben können auch verwendet werden. Auf einigen Bildern haben wir andere Schrauben verwendet.

### Kamera
Die vier M2x8 Schrauben durch die Befestigungslöcher der Kamera stecken und von hinten mit der Kunststoff-Mutter sichern. Die Mutter dient als Distanz und elektrische Isolation. Nicht ganz festziehen, die Schraube muss sich noch drehen lassen.
Die Kamera mit den Schrauben durch den Print mit den IR LED Stecken, Kamera und LED müssen in die gleiche Richtung schauen. <br>

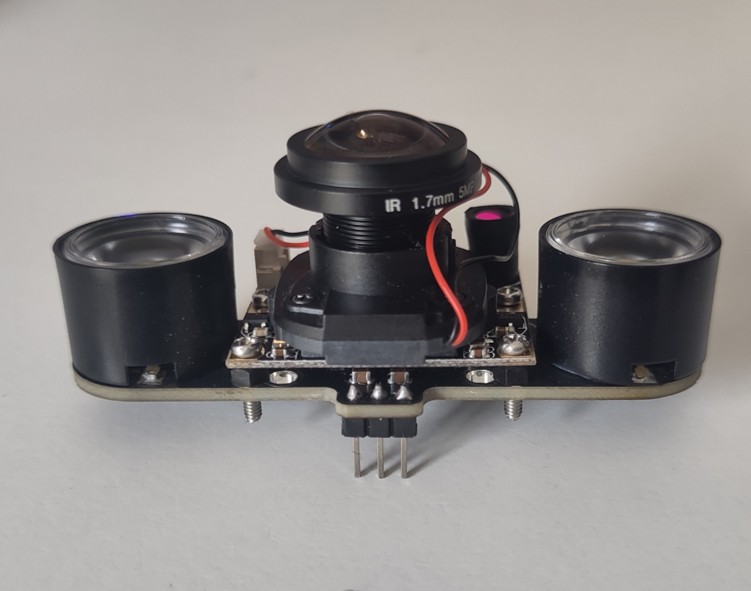
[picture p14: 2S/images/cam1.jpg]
Kamera auf Print
 

Nun Kamera und IR-LED Print mit den vier Schrauben am gedruckten Kopf befestigen.

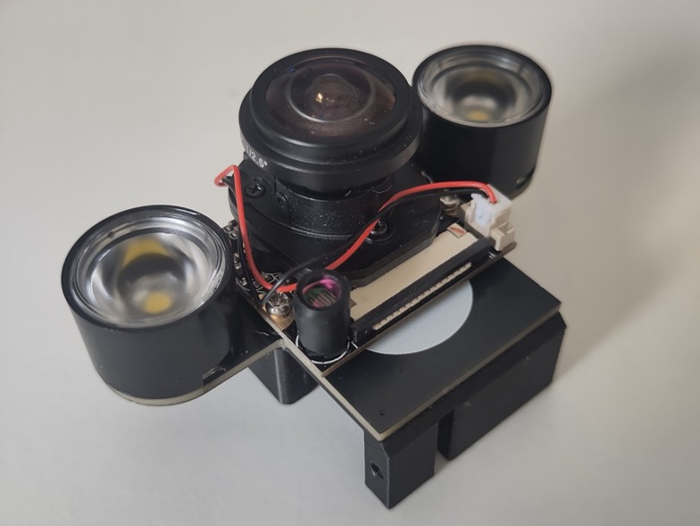
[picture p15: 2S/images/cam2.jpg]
Kamera an Kopf befestigen
 

### Nicken

Servo von hinten ins gedruckte Kopfteil montieren und von der Seite mit zwei M2x14 Schrauben befestigen

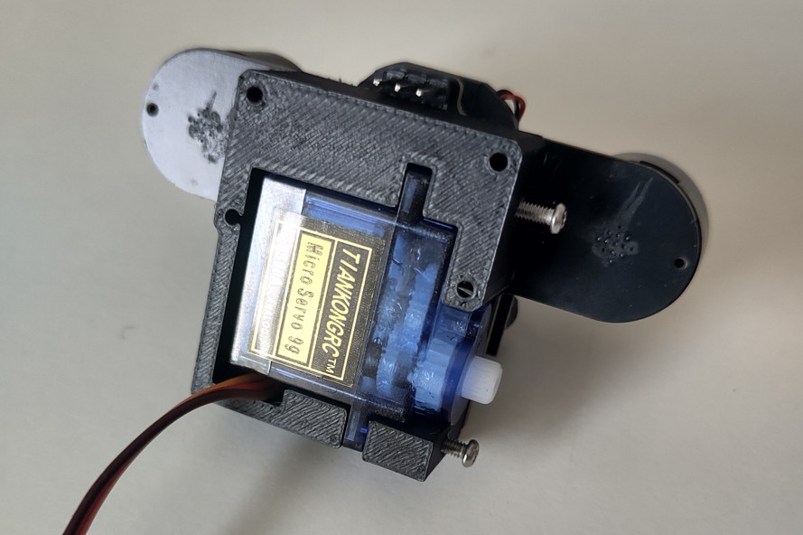
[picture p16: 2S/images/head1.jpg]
Servo in Kopf
 

### Kopf Schütteln

U-förmiges Druckteil mit einem einseitigen und dem doppelseitigen Servohorn bestücken. Servo zum Kopfschütteln von unten an das u-förmige Druckteil befestigen.

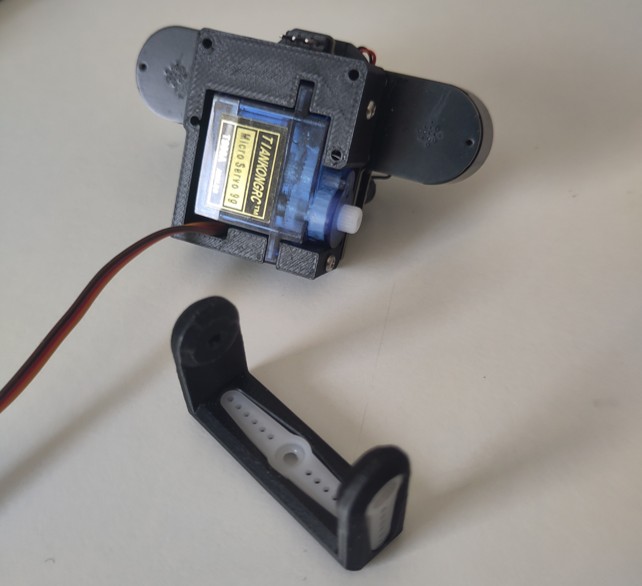
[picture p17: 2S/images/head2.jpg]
Teile vorbereiten
 

### Kompletter Kopf

Druckteil inkl. Servo am Kopf befestigen und von beiden Seiten mit einer Schraube fixieren.

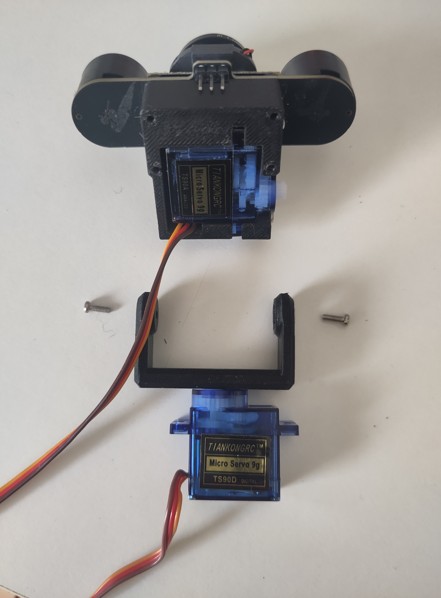
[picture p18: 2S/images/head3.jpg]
Kopf komplett
 

### Greifer zusammenbauen

Servohorn einseitig in Greifarm links einbauen. 

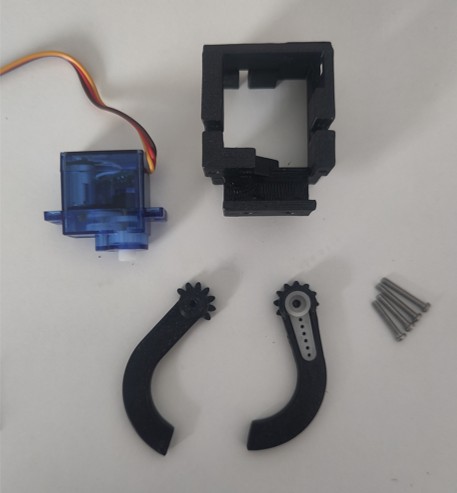
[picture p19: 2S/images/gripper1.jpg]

Das Servokabel durch das Druckteil fädeln wie im Bild.

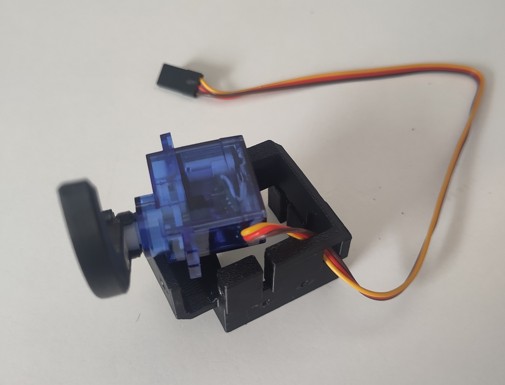
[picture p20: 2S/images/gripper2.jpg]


Die beiden Greifarme platzieren und mit den M2x12 Schrauben befestigen. Auf symmetrische Montage der Greifarme achten.

Servo mit 2x M2x14 am Halter Greifer befestigen.

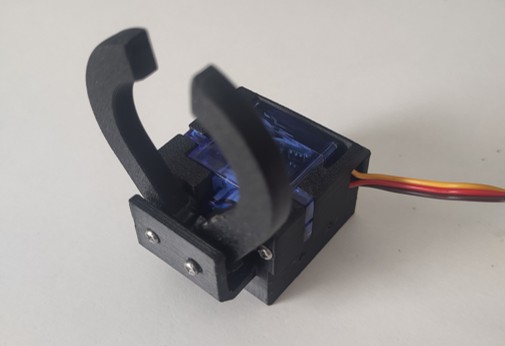
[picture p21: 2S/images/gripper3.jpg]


Den Halter Greifer und Kopf zur Hand nehmen. Ein einseitiges Servohorn im Druckteil einbauen. Servo mit Abtriebswelle gegen oben in Druckteil einbauen und mit 2x M2x14 am Druckteil befestigen.

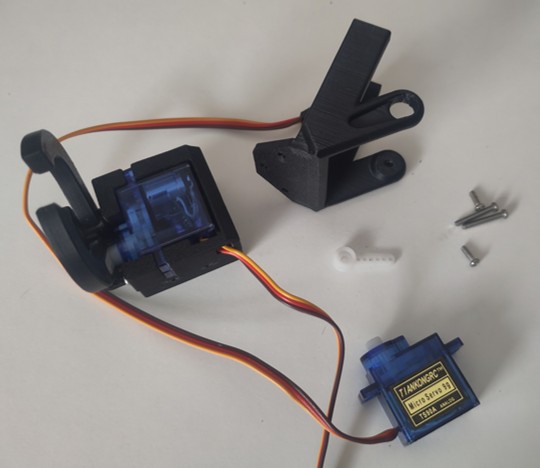
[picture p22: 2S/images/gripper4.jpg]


### Kopf und Greifer an Halter bauen

Ganzer Greifer in den Halter Greifer und Kopf einbauen und von beiden Seiten eine je eine M2x5 Schraube verbauten. Nicht zu stark anziehen, der Greifer muss sich noch leichtgängig heben und senken lassen.

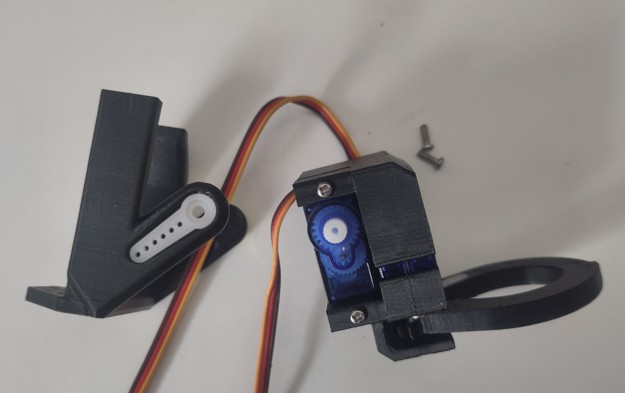
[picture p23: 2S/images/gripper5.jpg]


Ganzer Kopf mit zwei M2x5 Schrauben am Halter Greifer und Kopf befestigen. Sicherstellen, dass die Drehachse zum Kopf Schütteln in der Mitte der Baugruppe ist, sonst ist der Kopf daneben :-)

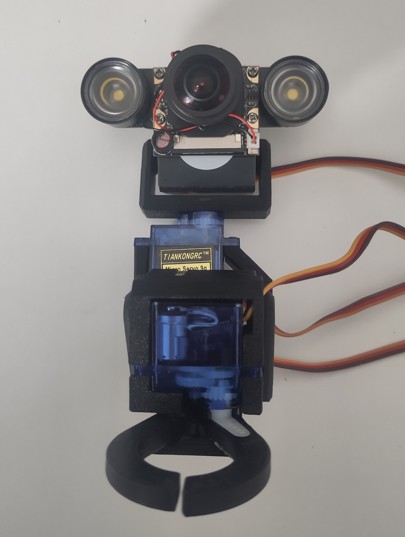
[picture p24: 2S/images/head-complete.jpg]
Kopf und Greifer


[⬆️ Zurück zum Inhaltsverzeichnis](#inhalt)

## 4.7 Finale Fertigstellung

Nun kann die Greifer- und Kopf-Baugruppe mit dem Body verbunden werden. Dazu den Deckprint mit Pi wieder vom Body ziehen (Vorsicht, dass die Verindungspins nicht verbiegen, wenn nicht gerade gegen oben gezogen wird).
Die G&K-Baugruppe kann nun unter den Baseprint geschoben und mit drei Schrauben M2.5x12 befestigt werden.

LTE / 4G Stick in 90° Winkelstecker stecken.
Der Roboter sollte nun betriebsbereit sein.

Steuere über die Vigibot-Website, überprüfe jeden Servoweg und stelle die Servohörner bei Bedarf neu ein. Ein Klick auf das Stopp-Symbol (Quadrat), stellt die Servos in die Mittelstellung. 

### Aufkleber auf dem Roboter

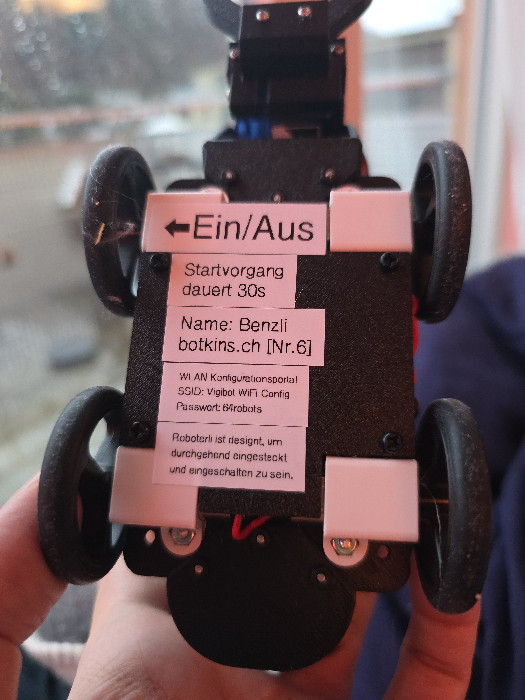
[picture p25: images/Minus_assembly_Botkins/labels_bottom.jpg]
labels_bottom
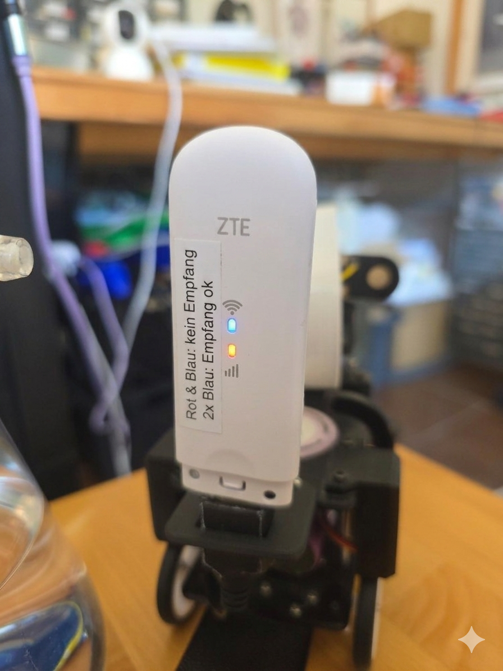
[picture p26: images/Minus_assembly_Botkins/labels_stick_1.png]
stick_1
 
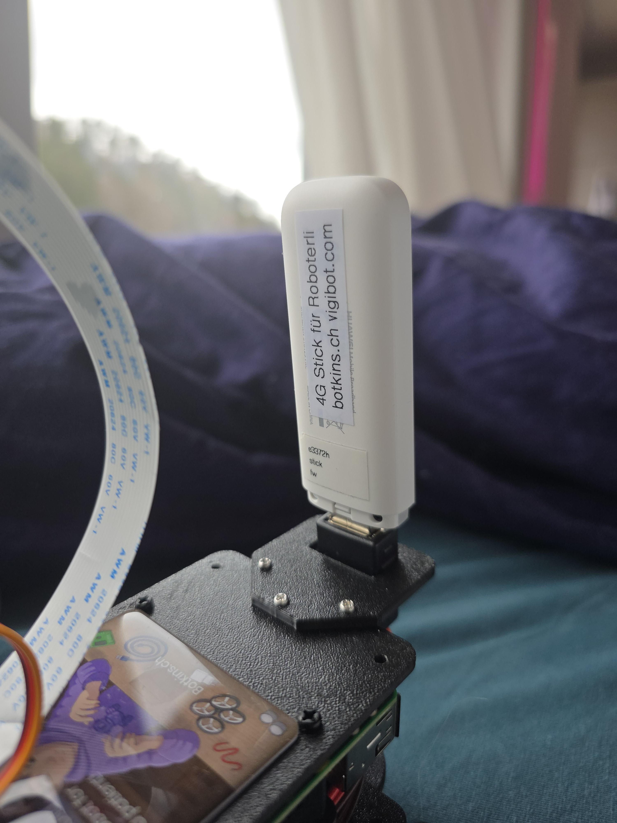
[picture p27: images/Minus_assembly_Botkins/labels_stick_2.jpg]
Stick 2


Um die Bedienung des Roboters durch die Nutzer zu vereinfachen, wird empfohlen, folgende Aufkleber zu drucken und anzubringen. Die mit ** Text ** geführten Ausdrücke müssen passend zu eurem Roboter angepasst werden. Die Schriftgrösse so anpassen, dass die Aufkleber Platz haben. Beim Hinweis zum LED-Farbcode des 4G Sticks muss auf den Typ des Sticks geachtet werden.

| Nr. | Benennung | Text  | Position am Roboter |
| --- | --- | --- | --- |
| 1 | Name | *Name: ** NAME ** botkins.ch [Nr. ** Roboternummer **]*| oben/unten auf dem Roboter |
| 2 | Startvorgang | *Startvorgang dauert 30s* | oben/unten auf dem Roboter |
| 3 | Hinweis Betrieb | *Roboterli ist designt, um durchgehend eingesteckt und eingeschaltet zu sein.*  | oben/unten auf dem Roboter|
| 4 | Empfang 4G Stick | *2x Blau: Empfang ok, Rot + Blau: kein Empfang* | auf dem 4G Stick |
| 5 | Hinweis 4G Stick | *4G Stick für botkins.ch vigibot.com* | auf dem 4G Stick |
| 6 | Ladehinweis | *Roboter vorne rechts mit USB-C laden* | - |
| 7 | WLAN Konfig | *Zum Verbinden mit WLAN Robo einschalten und mit Netzwerk "Vigibot WiFi Config" verbinden* | oben/unten auf dem Roboter |

[⬆️ Zurück zum Inhaltsverzeichnis](#inhalt)

## 4.8 Optionale Schritte

Diese Schritte sind nützlich, wenn Balena WiFi installiert werden soll. Kommt das Kit von Botkins, sind die optionalen Schritte breits vorinstalliert.

### apt repositories aktualisieren

<details close>
<summary>[Diesen Abschnitt anzeigen]</summary>

Um Dinge installieren zu können, müssen die Quellen für `apt` aktualisiert werden, da die ursprünglichen Paketquellen nicht mehr verfügbar sind.

1. raspi.list anpassen

```Shell
sudo nano /etc/apt/sources.list.d/raspi.list
```

Kommentiere alle vorhandenen Zeilen aus (mit # am Anfang der Zeile)
und füge folgende Zeilen ein:

```
deb http://legacy.raspbian.org/raspbian/ buster main contrib non-free rpi
deb http://archive.raspberrypi.org/debian buster main
```

Speichern (PuTTY):
Strg+O → Enter → Strg+X

1. sources.list anpassen

```
sudo nano /etc/apt/sources.list
```

Kommentiere hier ebenfalls alle vorhandenen Zeilen aus.

Speichern (PuTTY):
Strg+O → Enter → Strg+X

1. Paketlisten aktualisieren

```
sudo apt update
```

Danach sollte apt korrekt funktionieren.

</details>

### WLAN Unterstützung Einrichten

<details close>
<summary>[Diesen Abschnitt anzeigen]</summary>

Mit diesem Abschnitt kannst du deinem Roboter ermöglichen, sich per WLAN mit deinem Netzwerk zu verbinden. Wir nutzen dazu das **balena** **`wifi-connect`-Tool**, das ein Captive-Portal auf dem Roboter startet.

Führe zuerst den obigen Abschnitt `apt repositories aktualisieren` durch, bevor du weiterfährst.

> ⚠️ Achtung: Während der Installation wird die bestehende WLAN-Verbindung getrennt.

1. Verbinde den Roboter über **Ethernet** mit deinem lokalen Netzwerk.

2. Öffne die [Vigibot Website](https://www.vigibot.com) und klicke **lange** auf das Roboter-Icon.
   * Notiere die **LAN-IP-Adresse** deines Roboters, die angezeigt wird.

3. Verbindung per SSH herstellen. Je nach Betriebssystem:

* **Windows:** Nutze z.B. [PuTTY](https://www.putty.org/)
* **Android:** Nutze [Termius](https://play.google.com/store/apps/details?id=com.server.auditor.ssh.client) oder eine andere SSH-App.

Verbinde dich zu der notierten **IP-Adresse** des Roboters als Benutzer `pi` mit standart Passwort `raspberry`.

```Shell
ssh pi@ROBOT_IP
```

1. balena wifi-connect installieren

```
bash <(curl -L https://github.com/balena-io/wifi-connect/raw/master/scripts/raspbian-install.sh)
```

1. start\_BotkinsAP.sh erstellen

```
nano ~/start_BotkinsAP.sh
```

Füge folgenden Inhalt ein:

```
#!/usr/bin/env bash

printf 'Warten, um der WLAN verbindung Zeit zu geben, sich zu verbinden\n'
sleep 25

# Prüfen, ob bereits eine WLAN-Verbindung besteht
iwgetid -r
if [ $? -eq 0 ]; then
    printf 'Skipping WiFi Connect\n'
else
    printf 'Starting WiFi Connect\n'
    /usr/local/sbin/wifi-connect --portal-ssid "BotkinsAP" --portal-passphrase "03Sessel"
fi

sleep infinity
```

PuTTY Speichern: Strg+O, Enter, Strg+X.

1. Datei ausführbar machen

```
chmod +x ~/start_BotkinsAP.sh
```

1. rc.local anpassen
   Damit das WLAN-Captive-Portal automatisch beim Booten startet:

```
sudo nano /etc/rc.local
```

Füge vor `exit 0` folgende Zeile ein:

```
/home/pi/start_BotkinsAP.sh &
```

Speichern PuTTY: Strg+O, Enter, Strg+X.

1. Roboter neu starten

```
sudo reboot
```

Nach dem Neustart startet der Roboter automatisch das Captive-Portal `BotkinsAP` mit dem Passwort `03Sessel`.

Verbinde dein Smartphone zum Access Point `BotkinsAP`.

Es kann ca 60 Sekunden dauern, bis wifi-connect gestartet wird.
Öffne eine beliebige Website in einem Browser, das Captive-Portal wird dich automatisch zum Konfikurationsportal weiterleiten. Dort kannst du das gewünschte Heim-WLAN-Netzwerk aus einer Liste auswählen, womit sich der Roboter dann verbindet.

[⬆️ Zurück zum Inhaltsverzeichnis](#inhalt)

</details>

## 4.9 Funktionstest

Nun ist es Zeit für den finalen Check!
Teste die Funktionen des Roboters:

1. Roboter auf vigibot.com sichtbar mit korrektem Namen?
2. Alle Bedienelemente vorhanden? Wenn nicht > botkins Team fragen
3. Spannungsanzeige über dem Videostream vorhanden? Wenn nicht, botkins Team fragen
4. Bei Drücken auf das Stop-Symbol in der Steuerung bewegen sich alle Servos in die Mittelstellung. Stimmen die Mittelstellungen?
5. Steuerbefehle (vorwärts, rückwärts, links, rechts) funktionieren?
6. Alle Räder drehen?
7. Robo lässt sich präzise fahren, auch schnelles Drehen ist möglich?
8. Robo fällt beim abrupten Bremsen nicht vornüber?
9. Antriebsmotoren sind vor Staub und Zugriff geschützt?
10. Ruderhörner der Servos sind passgenau und spielfrei verbaut?
11. Kopf lässt sich drehen?
12. Kopf dreht symmetrisch in beide Richtungen? Wenn nicht > Servohorn lösen und in Ruhestellung einmitten
13. Nicken funktioniert?
14. Nicken symmetrisch in beide Richtungen? Wenn nicht > Servohorn lösen und in Ruhestellung einmitten
15. Der Greifer muss bis auf den Boden greifen können und sich komplett öffnen und schliessen lassen.
16. Der Greifer darf nicht „hängenbleiben“, was passieren kann, wenn die Schrauben zu weit/zu fest eingeschraubt sind. Dazu die Bewegungen ganz langsam durchführen.
17. Bei vollständigen Kopf- und Greiferbewegungen dürfen keine Kabel gezogen werden.
18. Verbinde dich mit Vigibot und stell die Kamera auf einen Text gerichtet scharf.
19. Schau mit dem Smartphone auf die "Augen", die IR-LEDs. Decke den runden Helligkeitssensor ab. Stelle die Helligkeit nun mit einem winzigen Schlitzschraubendreher auf das Minimum. Auf der anderen Seite wiederholen. Das verhindert übermässigen Akkuverbrauch.
20. Sind der Winkelstecker und der LTE/4G Stick und der Auffahrschutz montiert?
21. Teste den Roboter mit LTE/4G Stick, bei Dunkelheit, fahre und bewege Kopf oder Greifer bei niedrigem Akkustand (ca 3,3V – 3,5V), teste, ob Abstürze auftreten.
22. Ist die Ladebuchse des Roboters zugänglich?
23. Lass den Akku des Roboters vollständig entladen. Die Servos können sich leicht bewegen, aber der Roboter sollte nicht von selbst fahren.
24. Lass den Roboter eingeschaltet und schliesse bei vollständig entladenem Akku das Ladekabel an. Er sollte nicht in einer Boot-Schleife hängenbleiben.
25. Dreht das Drehlicht, wenn du dich mit dem Roboter verbindest?
26. Mirofon testen
27. Sind die Aufkleber angebracht?

[⬆️ Zurück zum Inhaltsverzeichnis](#inhalt)

# 5. Troubleshooting

<details open>
<summary>[Diesen Abschnitt verbergen]</summary>

Wenn du anhand der folgenden Tabelle keine Lösung findest, frage im Vigibot-Discord-Server (Tag @firened) oder in der Botkins Maker Signal-Gruppe nach.

| Problem | Mögliche Ursachen | Lösung | wichtig für |
| --- | --- | --- | --- |
| Der Roboter trennt sich sporadisch (alle paar Stunden oder Minuten) | (1) Schwache Batterie (2) Schlechter 4G-Empfang | (1) Aufladen (2) Einen anderen Standort ausprobieren | Nutzer |
| Der Roboter blinkt (visuell) und klickt (akustisch) alle paar Sekunden oder mehrmals pro Sekunde | Schwache Batterie | Roboter ausschalten und mehrere Stunden lang aufladen | Nutzer |
| Der Roboter trennt alle 5 Sekunden die Verbindung | Fehlerhafte Konfiguration von Vigibot | Bitten Sie Vigibot oder Botkins, die Online-Konfiguration der Roboter zu überprüfen | Nutzer |
| Das Video stottert, das Fahren wird unterbrochen, alle paar Sekunden erscheinen rote Balken auf der Website | Schlechter 4G-Empfang, zu geringe 4G-Bandbreite, Smartphone ist zu langsam/alt | Wählen Sie die Ansicht mit niedriger Bandbreite, probieren Sie einen anderen Standort aus und stellen Sie sicher, dass die mobile Datenübertragungsgeschwindigkeit mindestens „bis zu 50 Mbit/s“ beträgt, verwende ein anderes Gerät | Nutzer |
| Robo erscheint nicht, im vigibot.com, oder nur kurz | Ist der 4G/LTE Stick eingesteckt, aber es besteht keine Verbindung, wird nur auf WLAN umgeschaltet, wenn der Stick entfernt wird | Stick ausstecken, wenn über WLAN verbunden werden soll | Nutzer |
| Während der Montage ist der Roboter nach einem Neustart für einige Sekunden online und verschwindet dann | Keine 4G-Verbindung/Empfang | Ziehen Sie den 4G-Stick ab und versuchen Sie es mit WLAN oder Ethernet | Maker |
| Der Roboter lässt sich über ssh nicht verbinden, obwohl die IP-Adresse bekannnt ist | Firewall oder VPN blockt | Firewall oder VPN temporär ausschalten | Maker |
| ssh meldet trotz korrekter IP Adresse "  @@@ WARNING: REMOTE HOST IDENTIFICATION HAS CHANGED! @@@ ..." | Neues Image, alter Key | ssh-keygen -R 192.168.1.200 im Terminal eingeben und Enter, alter Key gelöscht. Erneut einloggen | Maker |
| Verbindung per ssh nicht möglich nach Aufspielen von neuem Image | Image hat Standardpasswort mitgegeben | Standardpasswort "raspberry" verwenden, um ssh zu starten | Maker |
| Spannung wird im vigibot Interface nicht korrekt angezeigt (2.5V) | Grund liegt je nach UPS am Pin, auf dem die Info an den PI gelangt. |Bsp: sudo nano /usr/local/vigiclient/sys.json > "INA219ADDRESS": 66 | Maker |

</details>

# 6. Credits

* Original Partlist: Vigibot
* Partlist Modifications: Botkins Charity Project
* Assembly Guide: Botkins Charity Project (unless otherwise noted)

[⬆️ Zurück zum Inhaltsverzeichnis](#inhalt)

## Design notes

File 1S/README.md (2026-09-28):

# Minus-Type 1S Vigibot Robot für Botkins

## Inhalt

<details open>
<summary>[Diesen Abschnitt verbergen]</summary>

* [Generelle Info](#generelle-info)
* [Voraussetzungen](#voraussetzungen)
* [Teileliste](#teileliste)
* [Minus-Type Zusammenbau](#minus-type-zusammenbau)
  * [1. Software Installieren](#1-software-installieren)
  * [2. Vigibot Online Konfiguration](#2-vigibot-online-konfiguration)
  * [3. UPS Solder Bridge](#3-ups-solder-bridge)
  * [4. Servostecker teilen](#4-servostecker-teilen)
  * [5. Spannungsversorgung](#5-spannungsversorgung)
  * [6. Signalleitungen verbinden](#6-signalleitungen-verbinden)
  * [7. Zusammenbau Motorplatte](#7-zusammenbau-motorplatte)
  * [8. Zusammenbau Kopf](#8-zusammenbau-kopf)
  * [9. Zusammenbau Greifer](#9-zusammenbau-greifer)
  * [10. Finale Fertigstellung](#10-finale-fertigstellung)
  * [11. Optionale Schritte](#11-optionale-schritte)
  * [12. Zusätzliche Bauanleitungen](#12-zusätzliche-bauanleitungen)
  * [13. Funktionstest](#13-funktionstest)
* [Troubleshooting](#troubleshooting)
* [Credits](#credits)

</details>

## Stand 2026-06-20

Das vigiUPSv3 ist nun verfügbar. Wir sind dabei die Updates von der upstream repo in diese Botkins Teileliste zu übernehmen.

## Stand 2026-02-13

Das UPS Bauteil ist aufgrund der mehreren neu gestarteten Roboterbauten im robot-maker Store ausverkauft.
Es gibt eine funktionierende Alternative, das «Waveshare UPS hat (D)» UPS, aber dies benötigt Modifikationen, sodass wir empfehlen auf das VigiUPSv3 zu warten, welches innert Monaten verfügbar sein sollte. Gib uns bescheid und wir schreiben dir sobald es verfügbar ist.

## Generelle Info

<details open>
<summary>[Diesen Abschnitt verbergen]</summary>

Dieser Leitfaden behandelt den Botkins V2. Weitere Verbesserungen sind in Arbeit und werden bald publiziert. Es ist geplant, ein komplettes Kit für Maker anzubieten. Es gibt aber keine Hürde oder Nachteil, einen Bot nach dieser Anleitung zu bauen. Die Funktionalität für die Patienten wird die selbe bleiben.

Erfahre mehr über das Botkins Charity Project:

* [botkins.ch](https://botkins.ch)&#x20;
* [Hackaday Page](https://hackaday.io/project/180558-botkins-charity-project)

Erfahre mehr über Vigibot:
Das französische Roboter-Projekt, wessen Software und Hardware Design Botkins benutzt.

* [Robot Maker Post](https://www.robot-maker.com/forum/topic/13010-what-is-vigibot-quest-ce-que-vigibot/)
* [Drive a robot Vigibot.com](https://www.vigibot.com/)

Als Basis dient die Standard Vigibot Minus-Type Version (siehe Bild, ein reines Botkin Bild folgt). Botkins ist zusätlich mit einem LTE/4G Stick ausgerüstet und kommt ohne Seitenarme aus.



* Wenn du für Botkins einen Roboter bauen möchtest, melde dich bei uns und wir senden dir die nötigen Informationen und den Zugang zu Resourcen.
* Als Maker kannst du die Farbe der 3D-gedruckten Teile selber wählen, sie ist nicht vorgegeben.
* Der Bau des ersten Roboters kann etwa 10 Stunden dauern, möglicherweise auch länger. Nach etwas Übung dauert der Bau etwa 3 Stunden pro Roboter.
* Einige Teile von Aliexpress können bis zu 5 Wochen fúr die Lieferung benötigen. Derzeit (2026) schlägt die Einstellung der Zahlungsmethode auf PayPal fehl, mit der Meldung "Sorry, some items are not available", bezahlen per Kreditkare funktioniert. Wähle [E-Mail order updates](https://www.aliexpress.com/p/edm-setting/index.html) vor dem Checkout ab, sonst bekommst du pro Bestellposition 3-5 Mails.

### Voraussetzungen

Du benötigst:

* Lötkolben (für die 4 Motoren und UPS-Brücke). (Wenn du nicht löten möchtest, kann vielleicht ein anderer Maker die Teile für löten).
* Internetzugang (SIM-Karte mit mobilen Daten, WLAN oder Ethernet-LAN), PC.
* Ein 3D-Drucker ist derzeit nicht erforderlich. Wenn du die 3D-Teile selbst drucken möchtest, werden M2- und M2,5-Schrauben und Muttern, die nicht in dieser Botkins-Teileliste aufgeführt sind, benötigt. Du findest sie in der upstream Vigibot-Teileliste in jedem der 3D-gedruckten Sektionen.
* Werkzeuge: Schraubenzieher, verstellbarer Schraubenschlüssel/Gabelschlüssel, Pinzette, Klebeband, ...

#### Geplante Verbesserungen am Leitfaden

Wir versuchen, den Bau der Botkins so einfach wie möglich zu gestalten, aber dieser Leitfaden ist nicht ganz so klar und einfach, wie wir es uns wünschen würden.
Verbesserungsvorschläge und Anregungen zu diesem Leitfaden sind sehr willkommen. Hilf uns, diesen Leitfaden durch Pull-Anfragen oder anderen Wegen zu verbessern.

#### Nächste Schritte (für Maker, die zur Verbesserung dieses Leitfadens beitragen möchten)

<details>
<summary>[Öffne diesen Abschnitt]</summary>
Bitte teile uns defekte Links oder Mängel (z. B. unklare oder fehlende Schritte) mit. 

* [x] Copy the parts from external guides into this guide and adjust accordingly for this specific build.
* [x] Translate the parts of the external guide from french to english.
* [ ] Move annotations and instructions that are littered through the partlist further down into the specific sections of the assembly guide. \[to be done by fire\_ned]
* [ ] extend the troubleshooting table
  * [ ] more scenarios
  * [ ] add pictures / gifs of led blinking patterns
  * [x] perhaps label whether that specific problem can happen during assembly (for makers) or during everyday use (for patients).
* [ ] add more function tests

</details>
</details>

## Teileliste

<details open>
<summary>[Diesen Abschnitt verbergen]</summary>
Zur einfacheren Lesbarkeit schlagen wir eine Bezugsquelle vor und listen Alternativen auf, wo vorhanden. Es ist euch selbstverständlich freigestellt, wo ihr die Teile beschafft.
Die meisten Teile können bei [robot-maker.com](https://www.robot-maker.com) beschafft werden

### Hauptteile

| Stk | Benennung | Shop | Alternative\* |
| --- | --- | --- | --- |
| 1 | Raspberry Pi 3B+ (or 3B), 1GB or 2GB | [Link](https://www.pi-shop.ch/raspberry-pi-3-model-b/) | [Alternative](https://www.robot-maker.com/shop/cartes-programmables/241-raspberry-pi-3b-plus-241.html) |
| 1 | Unlocked ZTE MF79 4G / LTE Stick | [Link](https://aliexpress.com/item/1005005844914823.html) | Huawei E3372h (Modell -153, -320 oder -607 |
| 1 | USB - USB 90° adapter | [Link, "Color : Down Angle Black"](https://aliexpress.com/item/1005003690522920.html) | - |
| 1 | USB bracket holder | [Link](https://www.robot-maker.com/shop/impression-3d/261-service-impression-3d-pla-261.html) | - |
| 1 | USB Microphone "Super AI". Die meisten anderen verfügbaren USB-Mikrofone sind leider entweder zu leise oder rauschen | [Link](https://www.robot-maker.com/shop/composants/446-microphone-usb-446.html) | [BOYA "Color : BY-M100UA"](https://aliexpress.com/item/1005004133896137.html) |
| 1 | 8-64GB "Endurance" Typ MicroSD Karte | [Link](https://www.robot-maker.com/shop/composants/91-carte-sd-32go-91.html) | [Alternative](https://www.berrybase.ch/sandisk-high-endurance-microsdhc-uhs-i-u3-speicherkarte-adapter-32gb) |
| 1 | Falls keinen vorhanden: CardReader für microSD | [Link](https://www.pi-shop.ch/sandisk-card-reader-usb-3-0-reader) | nach Belieben |
| 1 | Weitwinkelkamera mit Infrarot-Filter | [Link](https://www.robot-maker.com/shop/capteurs/311-camera-raspberry-pi.html) | [Alternative: "Color : Option 10"](https://aliexpress.com/item/1005004276506212.html) |
| 1 | 30cm Verbindungskabel für Kamera (zum ersetzen des kurzen Originals) | [Link](https://www.robot-maker.com/shop/composants/329-nappe-raspberry-pi.html#/92-longueur-30cm) | nach Belieben |
| 1 | Li-Ion Akku 1S2P 6800mAh | [Link](https://www.robot-maker.com/shop/alimentation/383-batterie-lithium-ion-1s2p-ncr-383.html) | Li-ion 1S2P 5-7Ah |
| 2 | 6A 67W Fast USB Charger | [Link, "Plug Type: EU Charger and Cable"](https://aliexpress.com/item/1005006632595521.html) | - |
| 1 | USB Kabel magnetisch | [Link, "Color : \*\* type c", "Length : 1m(3.3ft)"](https://www.aliexpress.com/item/4001224959039.html) | [Alternative Kabel](https://www.robot-maker.com/shop/alimentation/608-cable-usb-magnetique-data-608.html) + [Alternative Stecker "USB C"](https://www.robot-maker.com/shop/alimentation/609-embout-magnetique-micro-usb-ou-usb-c-rechargedata-609.html) |
| 1 | USB-A zu USB-C Kabel | [Link, "Color : A-C \*\* ", "Length : 1m"](https://aliexpress.com/item/1005008279278619.html) | nach Belieben |
| 1 | Active Buzzer 3V/5V, verbinde zwischen GND (kurzer Pin) und GPIO 18 | [Link, "activ"](https://www.robot-maker.com/shop/accessoires-robotiques/487-buzzer-5v-487.html) | [Alternative, "3v"](https://www.aliexpress.com/item/4000829554492.html) |
| 1 | Etwas Klett-Tape zum Befestigen der Batterie | [Link, "White 1Meter", "25mm Wide"](https://www.aliexpress.com/item/1005006680575466.html) | - |
| 1 | Falls noch keinen Vorhanden: Sekundenkleber | [Link, "1ML x10pcs"](https://aliexpress.com/item/1005008238433750.html) | - |
| 1 | Strommangement vigiUPSv2 | [Link](https://www.robot-maker.com/shop/alimentation/429-ups-hat-pour-raspberry-pi-429.html) | siehe "Hinweise zu Alternativen" |

Hinweis zum vigiUPSv2: Installiere die 2x Kamera-LEDs nicht, da sonst das Lademodul möglicherweise nicht mehr funktioniert, da der Akku aufgrund des zu hohen Leerlaufstromverbrauchs möglicherweise nie 100 % erreicht.

### \*Hinweise zu Alternativen:

Für gewisse Bauteile gibt es geprüfte Alternativen mit entsprechender Beschreibung.

<details>
<summary>[öffne diesen Abschnitt]</summary>

#### 4G / LTE Stick: Huawei E3372h

* Das neueste Modell "e3372h-325 (Brand: Brovi)" funktioniert nicht. Die älteren Modelle werden nicht mehr hergestellt.
* Finden Sie ein passendes Modell auf Secondhand-Plattformen. Das Modell muss „e3372h-153”, „e3372h-320” oder „e3372h-607” sein. Das Modell ist auf dem SIM-Steckplatz unter der Abdeckung aufgedruckt.
* Die funktionierenden e3372h-Modelle können zwei verschiedene Firmwares haben. (1) Die „hilink”-Firmware, die Plug\&Play-fähig ist und dem Pi eine IP-Adresse im Bereich 192.168.8.X zuweist. (2) Die „stick”-Firmware, die über ssh Verbindung via Terminal konfiguriert werden muss. [Anleitung](https://www.robot-maker.com/forum/topic/14850-how-to-use-the-e3372h-with-stick-firmware-instead-of-hilink-firmware/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) (Pi-Kenntnisse nötig)

#### UPS Alternativen

Seit Dezember 2025 wird das Geekworm UPS3 leider nicht mehr hergestellt.

* vigiUPSv3 sollte in einigen Monaten verfügbar sein. Bis dahin: Version aus der Teileliste (A) oder mit Mehraufwand (B)

Derzeit stehen folgende Alternativen zur Verfügung:

**A. vigiUPSv2**

Version aus der Teileliste, siehe oben

**B. Waveshare UPS hat (D)**

* <https://aliexpress.com/item/1005006100404260.html>

Funktioniert, benötigt jedoch einige Änderungen:

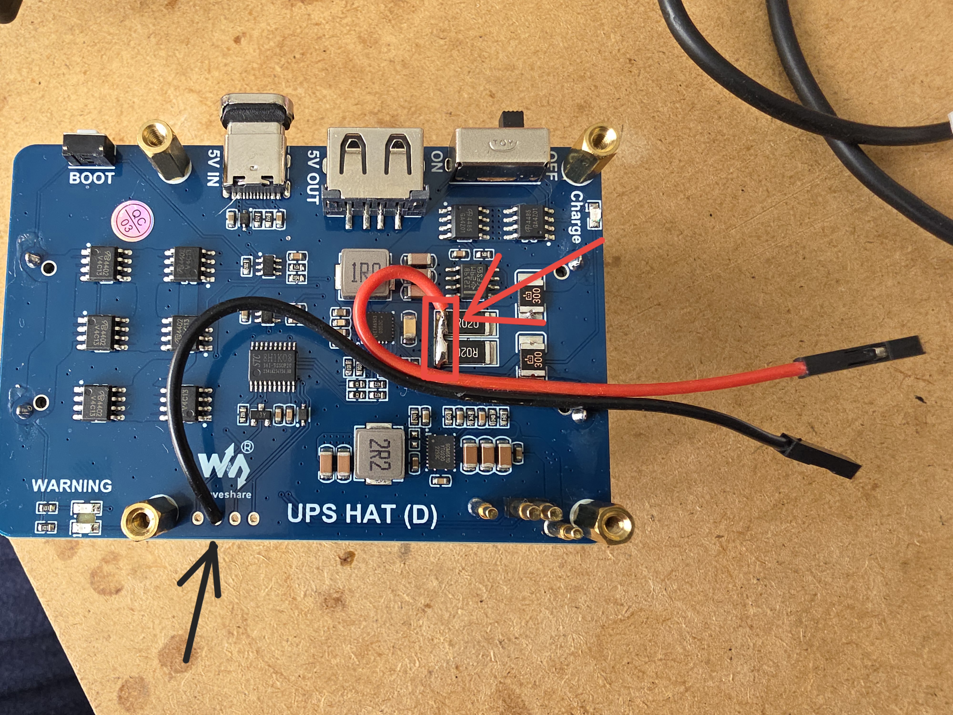
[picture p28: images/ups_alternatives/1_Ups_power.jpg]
1_Ups_power


* Löte die Stromkabel für Servos und Motoren an den abgebildeten Stellen an.
* Gib einen Tropfen Sekundenkleber hinzu, um die Drähte auf der USV-Platine zu befestigen.
* Kaufe 2x 21700 Liion-Zellen anstelle des Akkus aus der Teileliste.
* Kaufe zusätzlich 4x 20 mm M2,5 Metall-Sechskantständer.
* Nimm 1x abgewinkelten USB-Stecker „toUp“ anstelle des „toDown“ aus der Teileliste.

Um die Spannungs- und Strommessungen zum Laufen zu bringen, verbinde dich per ssh mit dem Roboter und konfiguriere ihn:

B.1) Spannungsmessung:

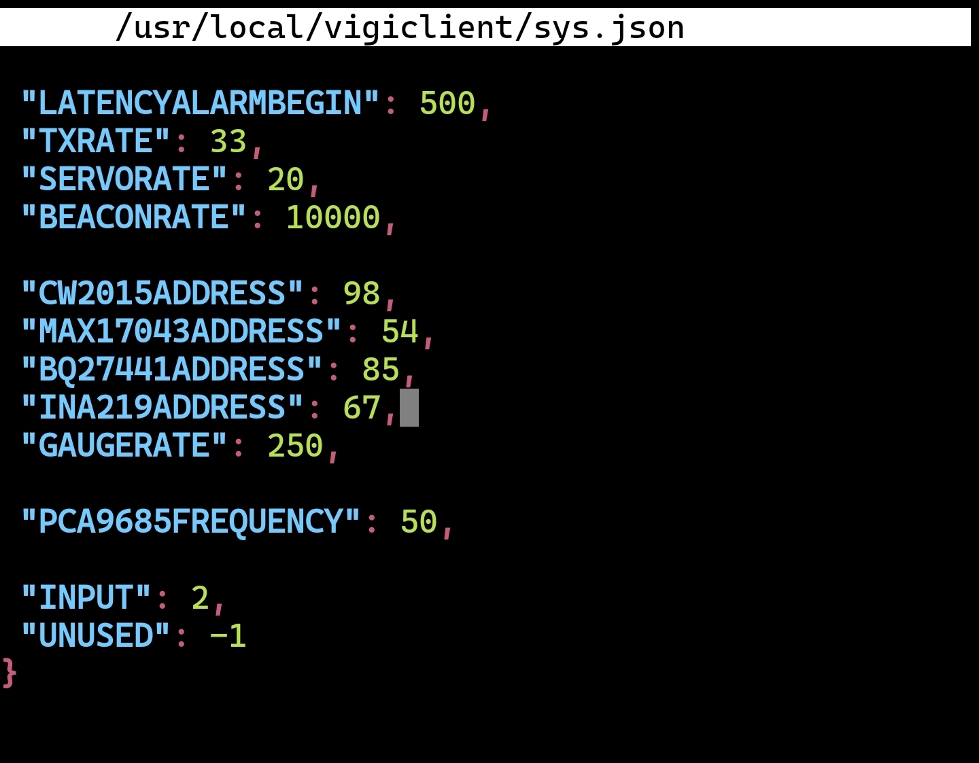
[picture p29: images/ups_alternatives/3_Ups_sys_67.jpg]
3_Ups_sys_67


```
sudo nano /usr/local/vigiclient/sys.json
```

* Ändern in `"INA219ADDRESS": 67,`

B.2) Die Strommessung funktioniert auch, aber ich würde empfehlen, diesen Schritt zu überspringen, da er nicht so wichtig ist.

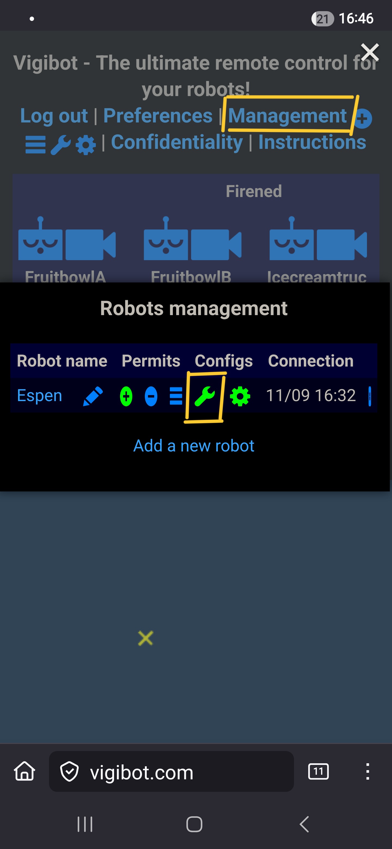
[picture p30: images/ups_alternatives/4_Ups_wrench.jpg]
4_Ups_wrench
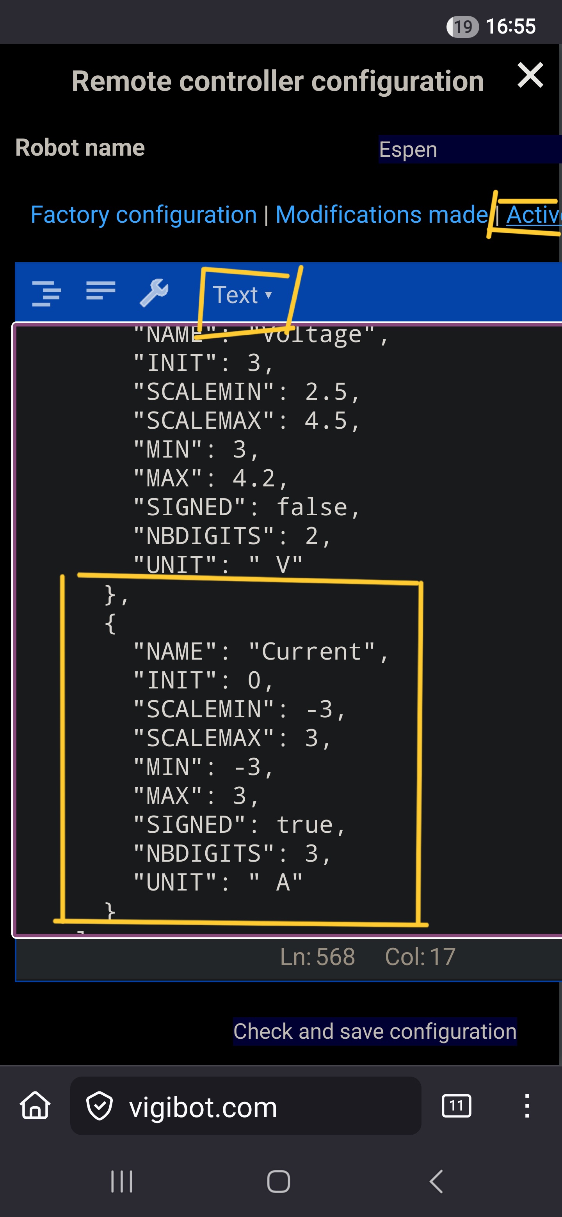
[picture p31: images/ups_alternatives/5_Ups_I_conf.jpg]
5_Ups_I_conf
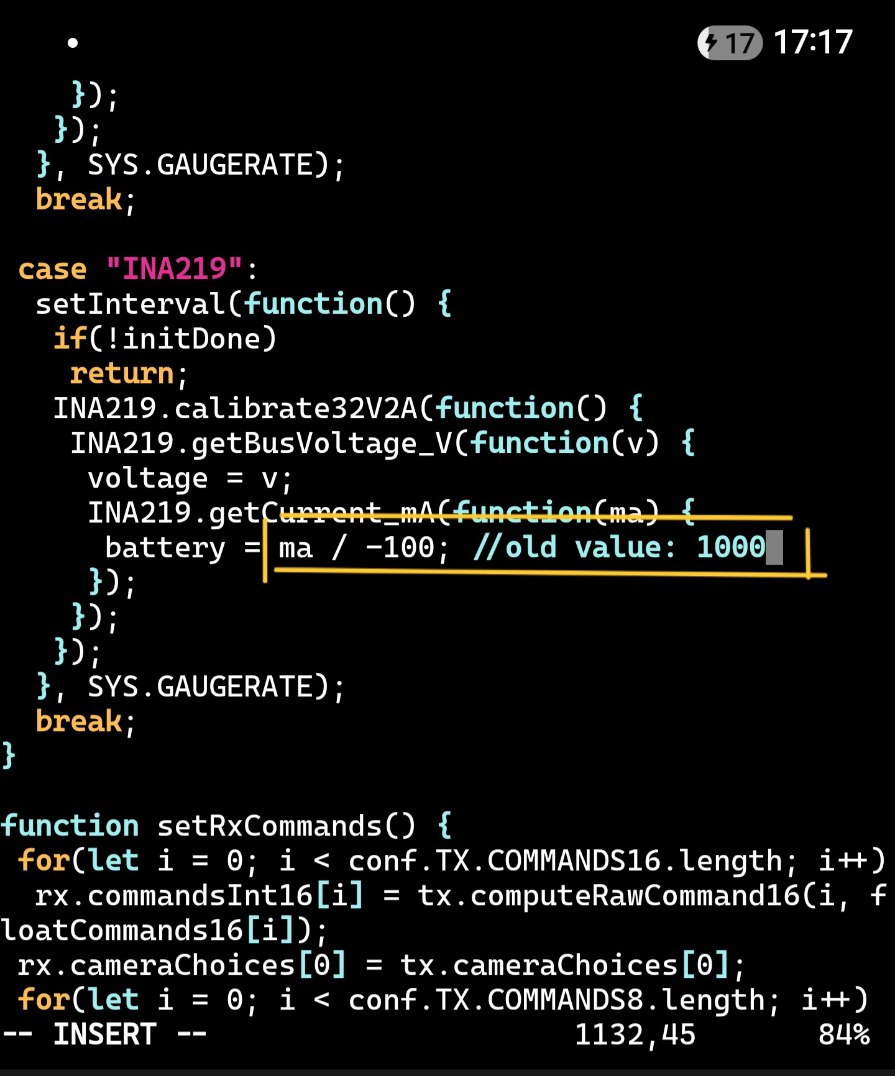
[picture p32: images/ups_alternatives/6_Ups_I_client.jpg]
6_Ups_I_client
\ 

* Nimm die Änderungen wie in den Bildern gezeigt vor
* Da der Shunt-Widerstand 1/10 des üblicherweise verwendeten Widerstands beträgt und Vin+ und Vin- vertauscht sind, muss der Code in `/usr/local/vigibot/clientrobotpi.js` geringfügig geändert werden. Ich bin mir nicht sicher, ob das sinnvoll ist, da eine Änderung des Codes meines Wissens nach zukünftige automatische Vigibot-Updates deaktiviert.

Stromverteilung für den Waveshare UPS hat (D)

| Stk  | Benennung | Shop | Alternative |
| ---- | --- | --- | --- |
| 1 | Splitter Board | [Link, "Color : 1 pcs"](https://www.aliexpress.com/item/1005006042011391.html) | - |
| 1 | PH2.0 zu 2 Pin Kabel 10cm  | [Link, "Color : 2P", "Length : 10CM"](https://www.aliexpress.com/item/1005002901249753.html) | - |
</details>

### Basisplatte Motor

| Stk | Benennung | Shop | Alternative |
| --- | --- | --- | --- |
| 8-16 | DuPont-Kabel | [Link, "30cm" or "20cm"](https://www.robot-maker.com/shop/composants/42-nappe-40-fils-femelle-femelle-42.html) | [Alternative, "Color : Mix 10 Color", "Connector Type : Female to Female", "Pins : 30cm"](https://www.aliexpress.com/item/1005005365866477.html) |
| 5 | Einzelne DuPont Pin Hüllen | [Link, "1P"](https://aliexpress.com/item/33035707563.html) | - |
| 1 | Komplettes Kit mit Druckteilen, <br> Schrauben, Muttern und Distanzbolzen | [Link](https://www.robot-maker.com/shop/kits-robots/425-kit-chassis-4wd-minus-425.html) | - |
| 4 | Pololu 100:1 Getriebemotoren HP 6V <br> mit Kabeln zum selber löten | [Link](https://www.robot-maker.com/shop/moteurs-et-actionneurs/384-moteur-pololu-300-rpm.html) | [Alternative](https://www.pololu.com/product/1101) |
| 4 | Pololu Motorhalter Extended | [Link](https://www.robot-maker.com/shop/elements-mecaniques/385-support-moteur-pololu-long.html) | [Alternative](https://www.pololu.com/product/1089) |
| 4 | Pololu Räder 40x7mm <br> es gibt Radmodelle bei den 3D Daten <br> Durchmesser beachten kleiner 40mm | [Link](https://www.robot-maker.com/shop/elements-mecaniques/346-roue-pololu-40mm.html) | [Alternative](https://www.pololu.com/product/1454) |
| 1 | Feetech 2-Kanal Motortreiber <br> Kabel inkl. | [Link](https://www.robot-maker.com/shop/drivers-d-actionneurs/280-driver-convertisseur-moteur-cc-servomoteur.html) | - |

### Kopf-Teile

| Stk | Benennung | Shop | Alternative |
| --- | --- | --- | --- |
| 1 | Komplettes Kit mit Druckteilen, <br> Schrauben, Muttern und Distanzbolzen | [Link](https://www.robot-maker.com/shop/kits-robots/88-kit-tourelle-pan-tilt-88.html) | - |
| 1 + 1 Reserve | DM-S0090MD 180° oder 270° Metall Getriebe Servo 9g <br> (Kopf Schütteln) | [Link, "Color : 1PCS DM-S0090MD 180"](https://aliexpress.com/item/1005010339946695.html)  | [Alternative, "Color: 1PCS-270 Degree"](https://aliexpress.com/item/1005007890905728.html) |
| 1 + 1 Reserve | 180° Servo 9g <br> (Nicken) | [Link](https://www.robot-maker.com/shop/moteurs-et-actionneurs/18-servomoteur-9g-18.html) | |

Hinweis: Verwende die langen Schrauben, um die Servos auf dem Servohalter zu befestigen.

### Greifer-Teile

| Stk | Benennung | Shop |
| --- | --- | --- |
| 1 | Komplettes Kit mit Druckteilen, <br> Schrauben, Muttern und Distanzbolzen | [Link](https://www.robot-maker.com/shop/kits-robots/423-kit-pince-minus-423.html) |
| 2 | 180° Servo 9g | [Link](https://www.robot-maker.com/shop/moteurs-et-actionneurs/18-servomoteur-9g-18.html) |

Hinweis: Verwende die langen Schrauben, um die Servos auf dem Servohalter zu befestigen.

### Druckteile und Kleinteile, falls ihr selber druckt

In der Ordnerstruktur befinden sich die Druckteile in verschiedenen Formaten. Hier eine Auflistung der benötigten Teile in den jeweiligen Stückzahlen

<details>
<summary>[öffne diesen Abschnitt]</summary>

| Pos | Beschreibung | Benennung im Ordner | V2 | Bild |
| --- | --- | --- | :---: | :---: |
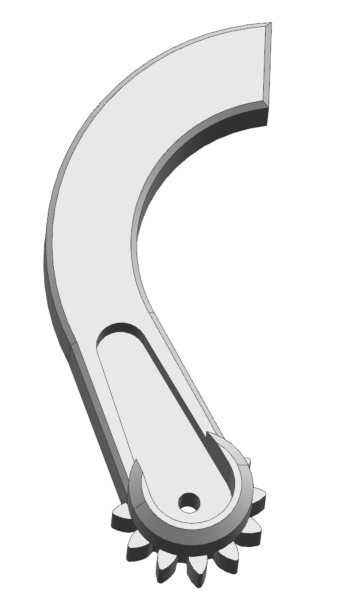
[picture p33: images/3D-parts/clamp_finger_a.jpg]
Finger A zu Greifer
| 1 | Finger A zu Greifer | stl/clamp\_finger\_a.stl | 1 Stk |  |
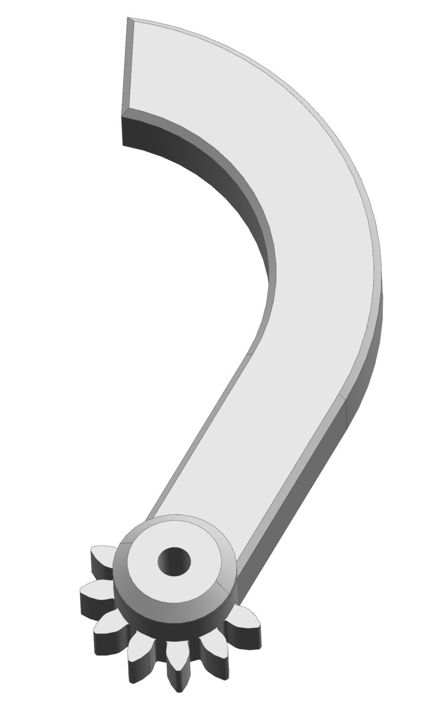
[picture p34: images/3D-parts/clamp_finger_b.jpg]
Finger B zu Greifer
| 2 | Finger B zu Greifer | stl/clamp\_finger\_b.stl | 1 Stk |  |
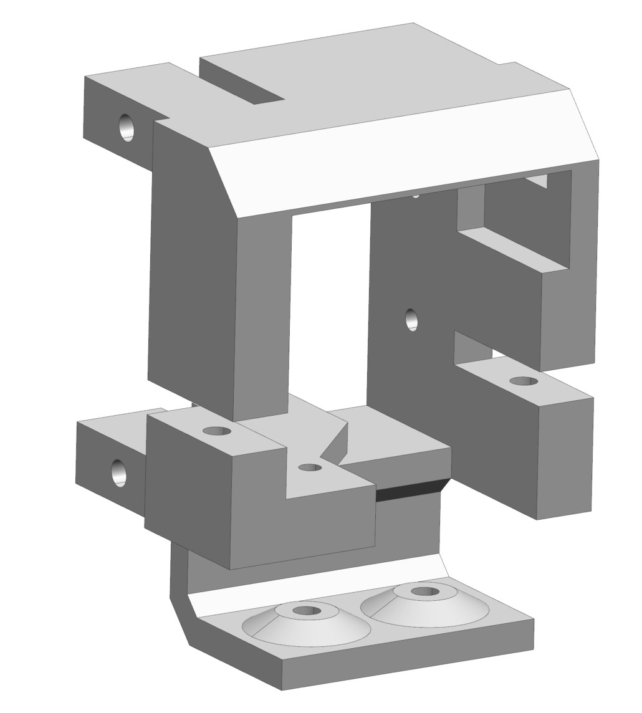
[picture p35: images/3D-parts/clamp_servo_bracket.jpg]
Servoaufnahme Greifer
| 3 | Servoaufnahme Greifer | stl/clamp\_servo\_bracket.stl | 1 Stk |  |
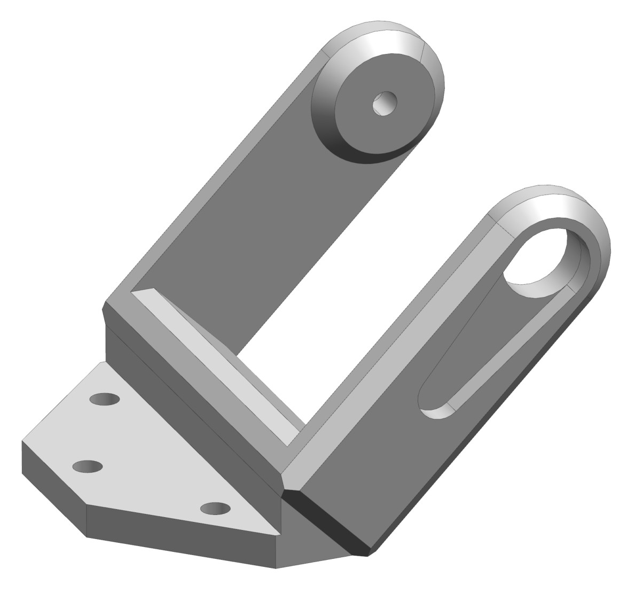
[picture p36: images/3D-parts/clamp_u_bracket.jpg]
Greiferhalter
| 4 | Greiferhalter | stl/clamp\_u\_bracket.stl | 1 Stk |  |
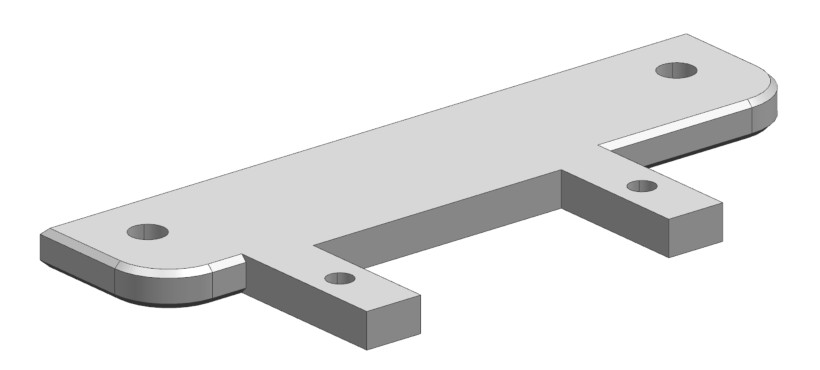
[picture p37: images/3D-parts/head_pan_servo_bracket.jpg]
Servohalter Kopf schütteln
| 5 | Servohalter Kopf schütteln | stl/head\_pan\_servo\_bracket.stl | 1 Stk |  |
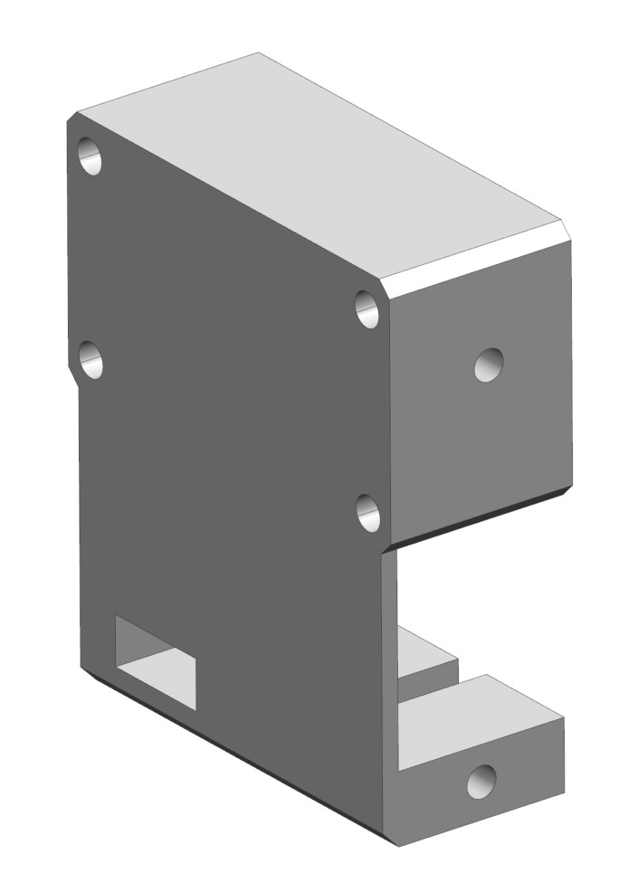
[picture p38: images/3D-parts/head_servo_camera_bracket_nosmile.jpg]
Kopf ohne Smile
| 6a  | Kopf ohne Smile | stl/head\_servo\_camera\_bracket\_nosmile.stl |  1 Stk <br> 6a oder 6b  |  |
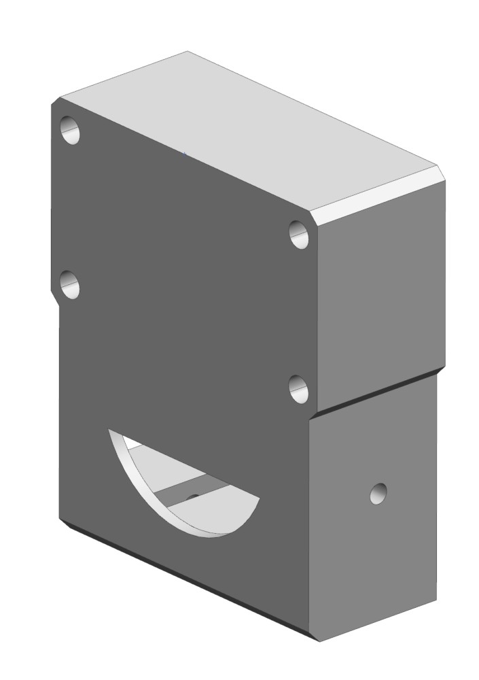
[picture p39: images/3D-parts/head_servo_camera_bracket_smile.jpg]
Kopf mit Smile
| 6b  | Kopf mit Smile | stl/head\_servo\_camera\_bracket\_smile.stl |  1 Stk <br> 6a oder 6b  |   |
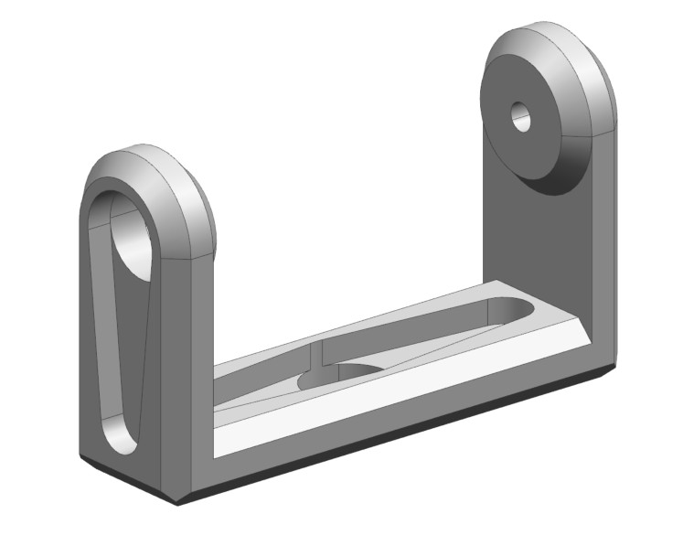
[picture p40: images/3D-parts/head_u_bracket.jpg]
Adapter Kopf schütteln
| 7 | Adapter Kopf schütteln | stl/head\_u\_bracket.stl | 1 Stk |  |
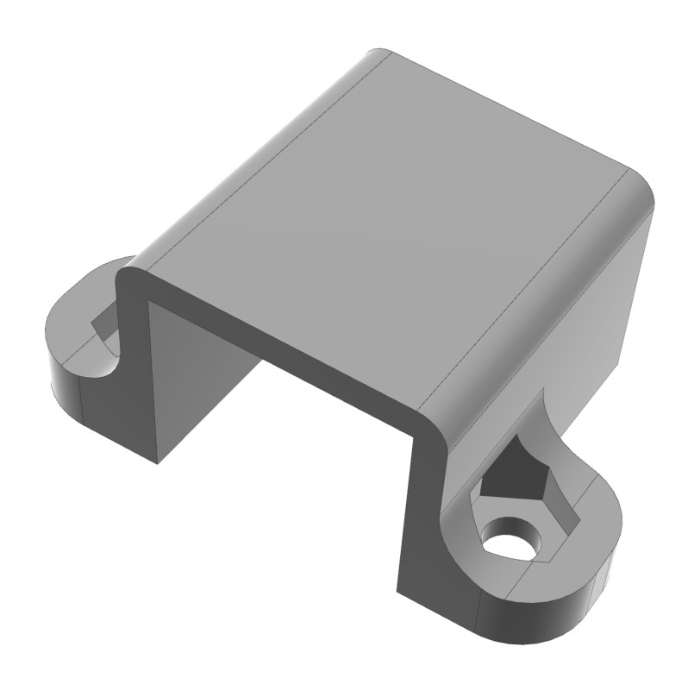
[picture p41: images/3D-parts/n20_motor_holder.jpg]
Motorhalter
| 8 | Motorhalter | stl/n20\_motor\_holder.stl | 4 Stk |  |
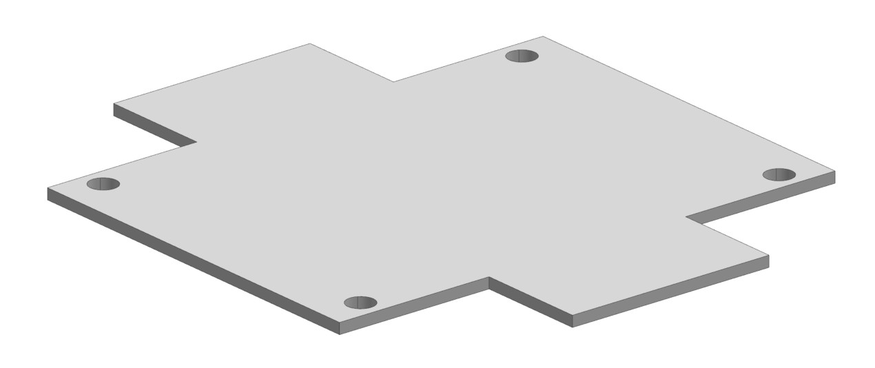
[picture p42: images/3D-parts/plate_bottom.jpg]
Bodenplatte
| 9 | Bodenplatte | stl/plate\_bottom.stl | 1 Stk |  |
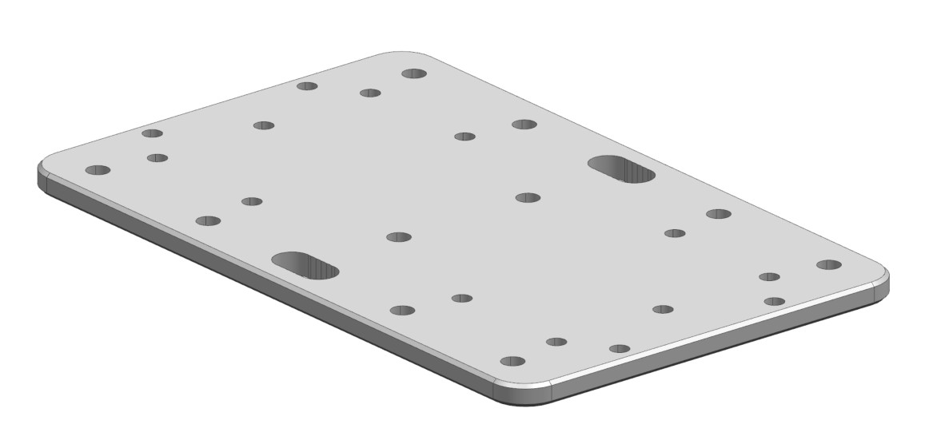
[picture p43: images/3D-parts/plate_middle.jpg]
Mittelplatte
| 10  | Mittelplatte = <br> Motorplatte | stl/plate\_middle.stl | 1 Stk |  |
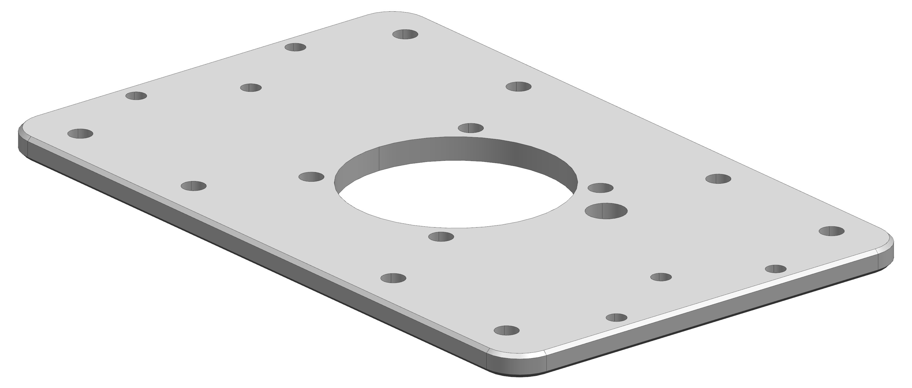
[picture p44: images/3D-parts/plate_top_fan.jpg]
Topplatte Fan
| 11a | Topplatte mit Lüfterloch | stl/plate\_top\_fan.stl | 1 Stk <br> 12a oder 12b |  |
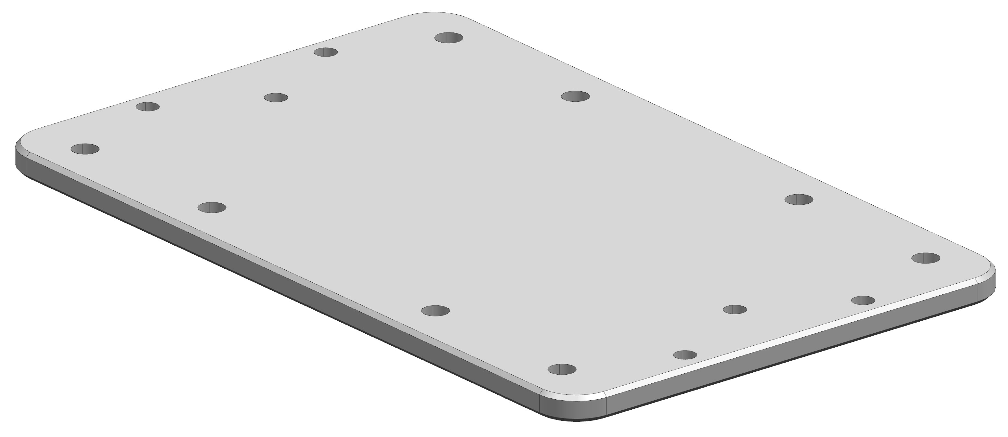
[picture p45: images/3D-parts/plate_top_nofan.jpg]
Topplatte No Fan
| 11b | Topplatte ohne Lüfterloch | stl/plate\_top\_nofan.stl | 1 Stk <br> 12a oder 12b |  |
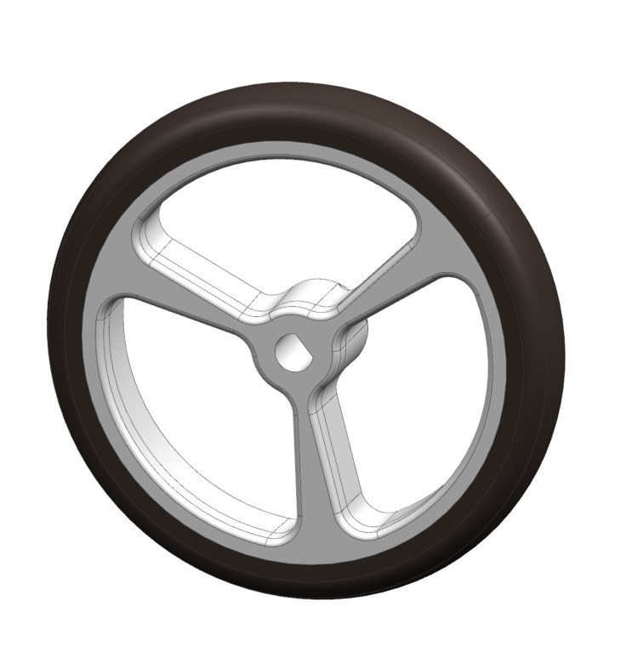
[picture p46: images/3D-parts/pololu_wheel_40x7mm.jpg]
Rad
| 12  | Rad 40 x 7mm | stl/pololu\_wheel\_40x7mm.stl | 4 Stk |  |
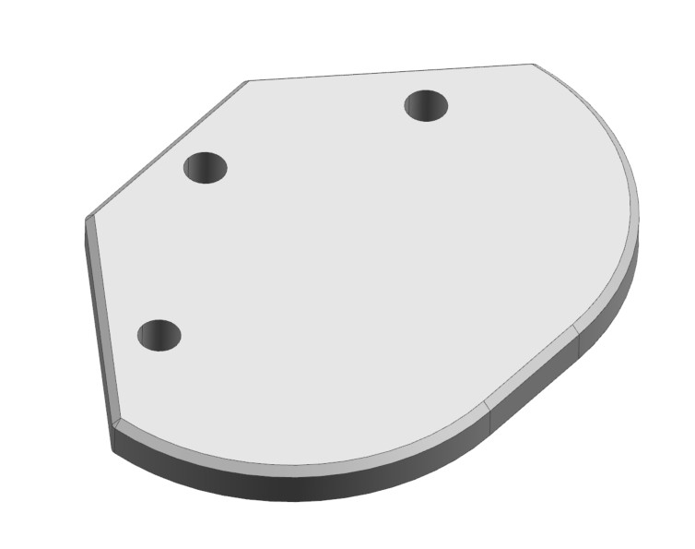
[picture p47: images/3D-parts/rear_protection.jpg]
Stossstange
| 13  | Stosstange hinten | stl/rear\_protection.stl | 1 Stk |  |
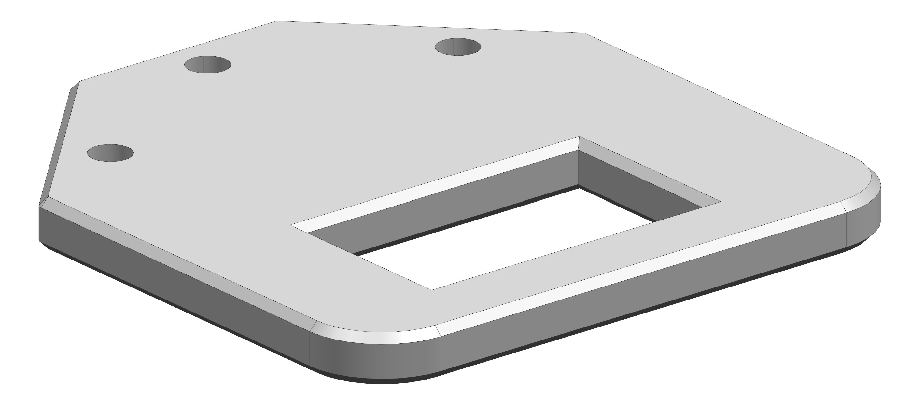
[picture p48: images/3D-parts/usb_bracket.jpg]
4G Stick Schutz
| 14  | 4G Stick Halter | stl/usb\_bracket.stl | 1 Stk |  |

### Kleinteile, falls ihr selber druckt

Anmerkung: Die Kamera <> Kopf Schrauben und Muttern müssen elektrisch leiten.

| Stk | Benennung | Dimmensionen  | wird verwendet für |
| --- | --- | --- | --- |
| 4 | Distanzbolzen M2.5 | Männchen 12mm | Pi <> UPS |
| 4 | Distanzbolzen M2.5 | Männchen 25mm | UPS <> Motorplatte |
| 4 | Distanzbolzen M2.5 | Weibchen 10mm | Grundplatte <> Motorplatte |
| 4 | Distanzbolzen M2.5 | Männchen 5mm  | Pi <> Topplatte |
| 10  | Schraube M2.5 | 6mm | 4x Topplatte <br> 4x Motorplatte <br> 2x Mittelplatte |
| 2 | Schraube M2.5 | 8 oder 10mm | für Motortreiber |
| 2 | Schraube M2.5 | 10 oder 12mm  | Pan Plate <> Roboter |
| 2 | Mutter M2.5 | - | 4x Motorplatte <br> 2x Mittelplatte <br> 2x Pan Plate |
| 4 | Schraube M2 | 20mm | 4x Kamera <> Kopf |
| 5 | Schraube M2 | 14 oder 16mm  | 2x 180° Servo <> Kopf <br> 5x Greifer |
| 1 | Schraube M2 | 10mm | 1x Greifer |
| 3 | Schraube M2 | 8mm | 3x Rückplatte <> Mittelplatte <br> 2x 270° Servo <> Pan Plate <br> 3x Greifer |
| 2 | Schraube M2 | 5 oder 6mm | ? |
| 15  | Mutter M2 | - | 3x Rückplatte <> Mittelplatte <br> 8x Kamera <br> 2x 270° Servo <> Pan Plate <br> 2x Greifer |

</details>
</details>

# Minus-Type Zusammenbau

<details open>
<summary>[Diesen Abschnitt verbergen]</summary>

## 1. Software Installieren

pi_cam<br>

Füge deinen Roboter bei Vigibot ganz einfach hinzu.
Du benötigst: einen Rapsery Pi (empfohlen 3B+), eine 16 oder 32 GB microSD Karte, eine Spannungsversorgung für den Pi, die Kamera mit dem passenden Kabel.
Mit wenigen einfachen Schritten kannst du deine Kamera auf [vigibot.com](https://www.vigibot.com/) live schalten:

* Erstelle auf [vigibot.com](https://www.vigibot.com/) einen Account.
* Klick auf "Management" und dann "Add a Robot". Wähle einen Namen für deinen Robter, den Roboter Typ Standard und ein Passwort für den Roboter. Das brauchen wir weiter unten gleich wieder, also merken.
* Lade das Image runter: [vigimage.zip](https://www.vigibot.com/vigimage/vigimage.zip) und entpacke die ZIP-Datei.
* Um die Image-Datei auf deine microSD Karte schreiben zu können, musst du diese mit dem PC verbinden (Kartenleser) und ein Tool zum Schreiben verwenden. Ich empfehle den Raspberry Pi Imager. Runterladen, installieren.
* Andere Tools wie das HDD Raw Copy Tool oder win32diskImager gehen auch. ApplePiBacker (Mac) oder balena etcher (Für Windows, Mac und Linux)
* Hinweis: Wenn du eine Karte grösser 32GB verwendest, musst du im Pi Imager zuerst das Modell 3 wählen, dann beim Betriebssystem löschen, um die Karte in FAT32 zu formatieren.
* Nach dem Ausführen des Pi Imager musst du das Modell des Pis auswählen, bei uns meist 3B+. Unter Betriebssystem wählst du zuunterst „Eigenes Image auswählen“, suchst das vigimage.img und wählst es aus. Dann wählst du die SD Karte als Zielmedium und bestätigst eine allfällige Überschreibewarnung. Starte den Schreibvorgang. Das dauert nun je nach Schreibgeschwindigkeit der Karte einige Minuten.
* Wenn das gemacht ist, öffne den /boot Ordner deiner SD Card. Windows: Sollte im Explorer der /boot Ordner nicht erscheinen, Drücke Win+R und gibt diskmgmt.msc ein. So gelangst du in die Datenträgerverwaltung. Wenn dort eine 100MB Partition gelistet ist, gib ihr über Rechtsklick > Laufwerkbuchstabe und -pfade ändern einen noch freien Buchstaben.
* Optional: Ändere die Datei "wpa\_supplicant.conf" mittels Rechtsklick und "in Editor anpassen" (Ändere die SSID „Demo“ und das Standardpasswort „Default“ entsprechend dem WLAN-Netzwerk, mit dem sich der Botkin verbinden soll. Tipp: Wenn (noch) kein 4G / LTE Stick vorhanden ist, kann mit dem Smartphone ein Hotspot eingerichtet werden. Vorteil: man kann den Botkin schon mitnehmen, wenn ein entsprechender Hotspot "mitreist". Nachteil: um auf den PI zuzugreifen via ssh, muss man im gleichen WLAN sein)
* Ändere die Datei "robot.json" gemäss dem zuvor gewählten Roboternamen und Roboterpasswort. ( Ändere den „Demo”-Benutzernamen und das „Standard”-Passwort)
* Installiere die SD-Karte im Raspberry Pi mit der installierten Kamera und schalte ihn dann ein (aufgrund des Kompilierungsprozesses dauert der erste Start einige Minuten, bevor der Roboter auf der Website erscheint (etwa 10 Minuten): Schalte den Raspberry Pi während dieser Zeit nicht aus).

Falls du auf den Pi zugreifen willst:
•	Der Pi und dein PC müssen in gleichen Netzwerk sein. Finde die IP Adresse des Pi raus (Verbindung über deinen Router (häufig hat der Router die IP 192.168.1.1) > Verbundene Geräte oder nutze eine App wie "Fing")
•	Win+R > „Powershell“ > Ausführen öffnet das Terminal
•	Gib im Fenster ein: ssh pi\@IP-ADRESSE (Ersetze die Adresse mit der Adresse des Pi, zB 192.168.1.146)
•	Das Terminal wird dich fragen, ob du sicher bist, eine Verbindung herstellen zu wollen. Schreibe „yes“ und bestätige
•	Verwende das Passwort, das du oben vergeben hast. Hast du robot.json nicht verändert, ist es „raspberry“.

* LTE/4G Mobile Data Stick:
* An einen Windows- oder Mac-PC anschliessen (die Webseite 192.168.8.1 wird geöffnet oder die App auf dem Speichermedium gestartet) und Datenroaming aktivieren.

## 2. Vigibot Online Konfiguration

#### Konfiguration der Fernsteuerung über Vigibot

Klicke auf der Vigibot Seite -> `Management` -> Werkzeug-Symbol (Remote controller configuration) -> `Modifications made` -> Wechsle von `Form` zu `Text` -> ersetze die `{}` mit dem folgenden Code:

<details>
<summary>[SHOW CODE BLOCK]</summary>

```JSON
{
  "BUTTONS": [
    {
      "ICON0": "vide",
      "ICON1": "",
      "TEXT": "",
      "ACTION": "",
      "SPECIAL": ""
    },
    {
      "ICON0": "vide",
      "ICON1": "",
      "TEXT": "",
      "ACTION": "",
      "SPECIAL": ""
    },
    {
      "ICON0": "vide",
      "ICON1": "",
      "TEXT": "",
      "ACTION": "",
      "SPECIAL": ""
    },
    {
      "ICON0": "avancer",
      "ICON1": "",
      "TEXT": "Forward",
      "ACTION": "IncrementForward",
      "SPECIAL": "yp"
    },
    {
      "ICON0": "vide",
      "ICON1": "",
      "TEXT": "",
      "ACTION": "",
      "SPECIAL": ""
    },
    {
      "ICON0": "suivant",
      "ICON1": "",
      "TEXT": "Next tool",
      "ACTION": "NextTool",
      "SPECIAL": ""
    },
    {
      "ICON0": "sirene0",
      "ICON1": "sirene1",
      "TEXT": "Buzzer",
      "ACTION": "Switch2",
      "SPECIAL": "i2"
    },
    {
      "ICON0": "lumicont0",
      "ICON1": "lumicont1",
      "TEXT": "Maximize the brightness and contrast",
      "ACTION": "Switch3",
      "SPECIAL": "i3"
    },
    {
      "ICON0": "gauche",
      "ICON1": "",
      "TEXT": "Left",
      "ACTION": "IncrementTurnLeft",
      "SPECIAL": "zn"
    },
    {
      "ICON0": "stopper",
      "ICON1": "",
      "TEXT": "Click to stop or drag to drive",
      "ACTION": "Brake",
      "SPECIAL": "st"
    },
    {
      "ICON0": "droite",
      "ICON1": "",
      "TEXT": "Right",
      "ACTION": "IncrementTurnRight",
      "SPECIAL": "zp"
    },
    {
      "ICON0": "centrer",
      "ICON1": "",
      "TEXT": "Reset tools",
      "ACTION": "ResetTools",
      "SPECIAL": ""
    },
    {
      "ICON0": "vide",
      "ICON1": "",
      "TEXT": "",
      "ACTION": "",
      "SPECIAL": ""
    },
    {
      "ICON0": "vide",
      "ICON1": "",
      "TEXT": "",
      "ACTION": "",
      "SPECIAL": ""
    },
    {
      "ICON0": "vide",
      "ICON1": "",
      "TEXT": "",
      "ACTION": "",
      "SPECIAL": ""
    },
    {
      "ICON0": "reculer",
      "ICON1": "",
      "TEXT": "Backward",
      "ACTION": "IncrementBackward",
      "SPECIAL": "yn"
    },
    {
      "ICON0": "capture",
      "ICON1": "",
      "TEXT": "Capture the last seconds of video",
      "ACTION": "",
      "SPECIAL": "capture"
    },
    {
      "ICON0": "precedent",
      "ICON1": "",
      "TEXT": "Previous tool",
      "ACTION": "PreviousTool",
      "SPECIAL": ""
    },
    {
      "ICON0": "vide",
      "ICON1": "",
      "TEXT": "",
      "ACTION": "",
      "SPECIAL": ""
    },
    {
      "ICON0": "vide",
      "ICON1": "",
      "TEXT": "",
      "ACTION": "",
      "SPECIAL": ""
    },
    {
      "ICON0": "lock0",
      "ICON1": "lock1",
      "TEXT": "Unlink remote control and video",
      "ACTION": "",
      "SPECIAL": "switchlock"
    },
    {
      "ICON0": "osd0",
      "ICON1": "osd1",
      "TEXT": "Toggle OSD",
      "ACTION": "",
      "SPECIAL": "switchosd"
    },
    {
      "ICON0": "vide",
      "ICON1": "",
      "TEXT": "",
      "ACTION": "",
      "SPECIAL": ""
    },
    {
      "ICON0": "dodo",
      "ICON1": "",
      "TEXT": "Put on standby",
      "ACTION": "Sleep",
      "SPECIAL": ""
    },
    {
      "ICON0": "vide",
      "ICON1": "",
      "TEXT": "",
      "ACTION": "",
      "SPECIAL": ""
    },
    {
      "ICON0": "vide",
      "ICON1": "",
      "TEXT": "",
      "ACTION": "",
      "SPECIAL": ""
    },
    {
      "ICON0": "vide",
      "ICON1": "",
      "TEXT": "",
      "ACTION": "",
      "SPECIAL": ""
    },
    {
      "ICON0": "exit",
      "ICON1": "",
      "TEXT": "Restart the client process",
      "ACTION": "ExitRobot",
      "SPECIAL": "confirm"
    },
    {
      "ICON0": "reboot",
      "ICON1": "",
      "TEXT": "Reboot the system",
      "ACTION": "RebootRobot",
      "SPECIAL": "confirm"
    },
    {
      "ICON0": "poweroff",
      "ICON1": "",
      "TEXT": "Power off the system",
      "ACTION": "PowerOffRobot",
      "SPECIAL": "confirm"
    }
  ],
  "COMMANDS": [
    {
      "NAME": "Camera control",
      "CAMERA": 0,
      "MIXING": 0,
      "GAINX": 80,
      "GAINY": 80
    },
    {
      "NAME": "Gripper control",
      "CAMERA": 0,
      "MIXING": 1,
      "GAINX": 80,
      "GAINY": 80
    },
    {
      "NAME": "250 Kbps - Camera control",
      "CAMERA": 1,
      "MIXING": 0,
      "GAINX": 80,
      "GAINY": 80
    },
    {
      "NAME": "250 Kbps - Gripper control",
      "CAMERA": 1,
      "MIXING": 1,
      "GAINX": 80,
      "GAINY": 80
    }
  ],
  "TX": {
    "COMMANDS16": [
      {
        "NAME": "Turret X",
        "INIT": 0,
        "SCALEMIN": -180,
        "SCALEMAX": 180,
        "MIN": -90,
        "MAX": 90,
        "CLAMPMIN": -20,
        "CLAMPMAX": 20,
        "SIGNED": true,
        "NBDIGITS": 2,
        "UNIT": "°"
      },
      {
        "NAME": "Turret Y",
        "INIT": 0,
        "SCALEMIN": -180,
        "SCALEMAX": 180,
        "MIN": -55,
        "MAX": 55,
        "CLAMPMIN": -40,
        "CLAMPMAX": 20,
        "SIGNED": true,
        "NBDIGITS": 2,
        "UNIT": "°"
      },
      {
        "NAME": "Gripper X",
        "INIT": 0,
        "SCALEMIN": -180,
        "SCALEMAX": 180,
        "MIN": -30,
        "MAX": 65,
        "CLAMPMIN": -20,
        "CLAMPMAX": 65,
        "SIGNED": true,
        "NBDIGITS": 2,
        "UNIT": "°"
      },
      {
        "NAME": "Gripper Y",
        "INIT": 0,
        "SCALEMIN": -180,
        "SCALEMAX": 180,
        "MIN": -40,
        "MAX": 80,
        "CLAMPMIN": 0,
        "CLAMPMAX": 45,
        "SIGNED": true,
        "NBDIGITS": 2,
        "UNIT": "°"
      }
    ]
  }
}
```

</details>

#### Hardware Konfiguration

Klicke auf der Vigibot Seite -> `Management` -> Zahnradsymbol (Hardware configuration) -> `Modifications made` -> Wechsle von `Form` zu `Text` -> ersetze `{}` mit dem folgenden Code:

<details>
<summary>[SHOW CODE BLOCK]</summary>

```JSON
{
  "CAMERAS": [
    {
      "TYPE": "",
      "SOURCE": 0,
      "WIDTH": 640,
      "HEIGHT": 480,
      "FPS": 30,
      "BITRATE": 1500000,
      "ROTATE": 180,
      "BRIGHTNESS": 50,
      "CONTRAST": -5,
      "BRIGHTNESSBOOST": 80,
      "CONTRASTBOOST": 100
    },
    {
      "TYPE": "",
      "SOURCE": 0,
      "WIDTH": 640,
      "HEIGHT": 480,
      "FPS": 30,
      "BITRATE": 250000,
      "ROTATE": 180,
      "BRIGHTNESS": 50,
      "CONTRAST": -5,
      "BRIGHTNESSBOOST": 80,
      "CONTRASTBOOST": 100
    }
  ],
  "COMMANDS8": [
    {
      "RAMPUP": 0,
      "RAMPDOWN": 0,
      "RAMPINIT": 0,
      "FAILSAFE": true,
      "SLEEP": true
    },
    {
      "RAMPUP": 15,
      "RAMPDOWN": 15,
      "RAMPINIT": 15,
      "FAILSAFE": true,
      "SLEEP": true
    },
    {
      "RAMPUP": 15,
      "RAMPDOWN": 15,
      "RAMPINIT": 15,
      "FAILSAFE": true,
      "SLEEP": true
    }
  ]
}
```

</details>

## 3. UPS Solder Bridge

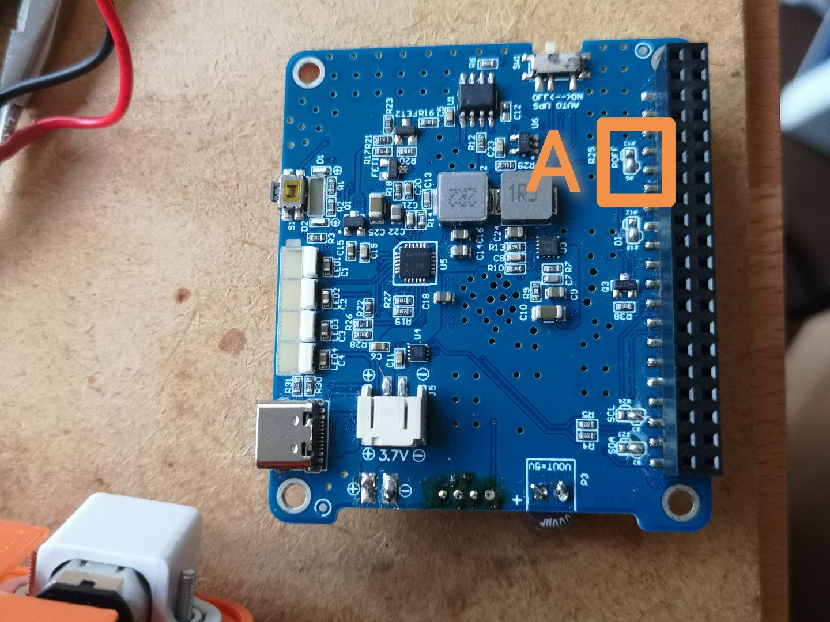
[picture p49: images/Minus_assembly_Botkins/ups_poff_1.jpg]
ups_poff_1


* A: Remove `POFF` solder bridge<br>

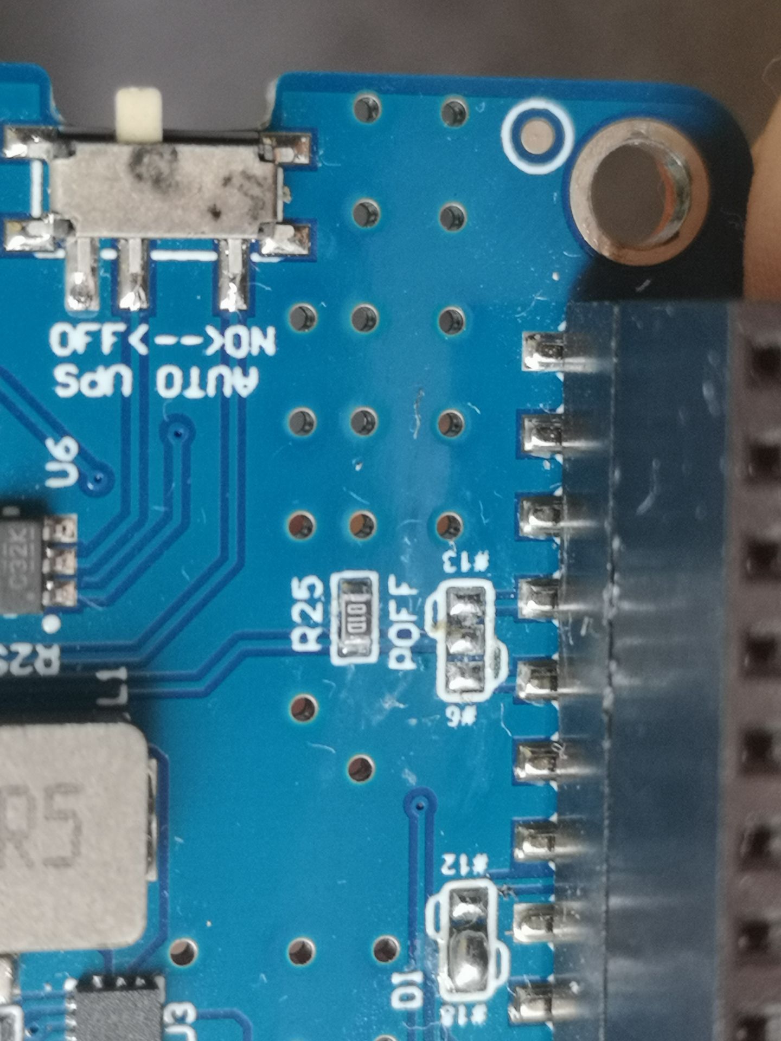
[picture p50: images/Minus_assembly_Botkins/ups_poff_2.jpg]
ups_poff_2
<br>

* set the `AUTO-UPS` switch to `OFF`

## 4. Servostecker teilen

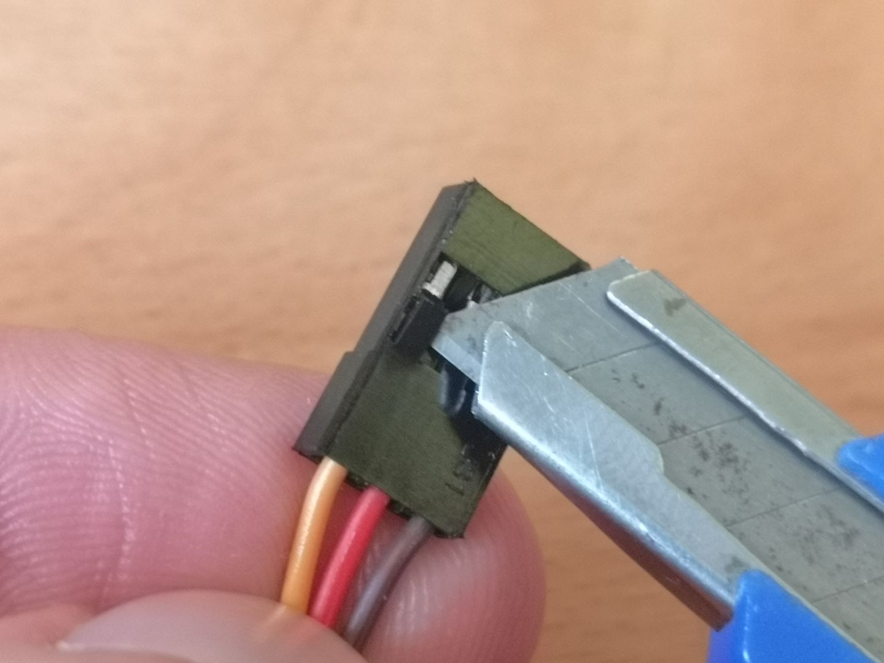
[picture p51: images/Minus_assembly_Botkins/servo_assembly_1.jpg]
servo_assembly_1

servo_assembly_2
servo_assembly_3
servo_assembly_4

* Die Servos werden in dieser Version über die Spannungsversorgungsprint mit Strom versorgt. Die Signalleitungen werden direkt auf dem Pi eingesteckt. Dazu müssen die Kabel "geteilt" werden.
* Hinweis zu Servokabelfarben: Pluspos ist immer rot. GND ist entweder schwarz oder braun. Die Signalleitung ist entweder orange, gelb, weiss oder blau. Kompliziert, ich weiss.
* Erstelle nun für jedes Servo einen Stecker mit zwei Polen (+ und GND) und eine einpolige Signalleitung. Um die Stecker einstecken zu können, entfernen wir die Kabel inkl. gecrimpte Buchsen und packen sie in neu Zweier-, resp. Einer-Kunststoffhüllen. Siehe Teileliste, die DuPont Buchsen.
* Split the signal (orange or white) wire off the 4x servos and 1x motor driver.

## 5. Spannungsversorgung

pdb_assembly_1 pdb_assembly_3 pdb_assembly_4<br>

* Wenn nötig, Polarität des PH2.0 Kabels anpassen, je nach USP<br>

pdb_assembly_5

* Baue den UPS auf den Raspberry Pi.
* Update 26.05.2025: Schneide den Batteriestecker ab (schneide + und - nacheinander ab, um die Batterie nicht kurzzuschliessen) und löte ihn an die Batterielötpads der USV. Die Servos und Motoren können wie auf den Fotos gezeigt mit Strom versorgt werden. Grund: Der Roboter kann sich zufällig oder bei nur teilweise geladener Batterie ausschalten. Ein weiteres Symptom ist, dass die gemessene Batteriespannung von 4,2 V auf 3,8 V oder weniger abfällt, wenn das Gerät vom Stromnetz getrennt wird. Es scheint, dass der kombinierte Widerstand der Batterieleistung, die über drei Stecker läuft, zu hoch ist.

## 6. Signalleitungen verbinden

wiring_assembly_1
pinout_ups
wiring_assembly_3<br>

Nun werden die Servos an der richtigen Stelle auf dem Pi eingesteckt:

* A: Kopf Schütteln : Head pan \[x] `GPIO 5 (physical pin 29)`<br>
* B: Nicken: Head tilt \[y] `GPIO 6 (physical pin 31)`<br>
* C: Greifer auf/zu: Gripper claw \[x] `GPIO 7 (physical pin 26)`<br>
* D: Greifer heben/senken: Gripper tilt \[y] `GPIO 8 (physical pin 24)`<br>

wiring_assembly_5<br>

* A: ESC Motortreiber
  * Linke Motoren `GPIO 26 (physical pin 37)`
  * Rechte Motoren `GPIO 27 (physical pin 13)`

Sollte ein Motor eine falsche Drehrichtung haben, Polarität der Motorkabel am Treiber andersherum anschliessen.

* Verwende das magnetische USB-Kabel, um die USV mit Strom zu versorgen. (Hinweis: Verwende ab sofort den Anschluss auf der USV-Platine – nicht auf der Raspberry Pi-Platine.)
* Testen Sie die Steuerung jedes Servos von Vigibot.
* Bevor Sie fortfahren, drücke `Stop ■` Drücke die Taste, um alle Servos zu zentrieren. Fahre den Bot über die Taste mit dem durchgestrichenen Steckersymbol im Vigibot Kontrollfeld herunter und ziehe den Akku und das USB-Kabel ab.

### Zusammenstellung aller PINS

Da die zu verwendenen PINs verstreut in der Beschreibung zu finden sind, hier eine Zusammenstellung:

| Beschreibung | GPIO | PIN Nummer |
| :--- | :--: | :---: |
| Kopf schütteln | 5  | 29 |
| Kopf nicken | 6  | 31 |
| Greifer auf / zu | 7  | 26 |
| Greifer auf / ab | 8  | 24 |
| Motor rechts |  27  | 13 |
| Motor links |  26  | 37 |
| Buzzer + |  18  | 12 |
| Buzzer GND | | 14 |

## 7. Zusammenbau Motorplatte

Benötigtes Material, enthalten in den Kits oder anhand der Kleinteile-Liste

* Motorplatte
* 4 Motoren mit angelöteten Kabeln, Länge ca. 12cm
* 4 Motorhalter mit Schrauben und Muttern
* Motortreiber mit Schrauben und Muttern

1. Befestigung der Motoren mit Motorhalten, je 2 Schrauben und 2 Muttern (von unten)

Middle plate assembly-1 Middle plate assembly-2
2\. Motortreiber mit zwei Schrauben und zwei Muttern an der Motorplatte befestigen

Middle plate assembly-3 Middle plate assembly-4
3\. Schlussendlich sollten die Kabel so aussehen wie im nächsten Bild. Die Motoren auf der gleichen Seite haben die Stecker jeweils nebeneinander. Die Verbindung zum Pi stellt ihr anhand der Beschriftung auf dem Treiber her. Linke Motoren `GPIO 26 (physical pin 37)`, rechte Motoren `GPIO 27 (physical pin 13)`<br>

Motor Plate complete <br>
4\. Auffahrschutz, Greiferhalter und Abstandshalter montieren. Länge siehe Tabelle unten

Middle plate assembly-5Middle plate assembly-6
Middle plate assembly-7Middle plate assembly-8
Middle plate assembly-9Middle plate assembly-10

| Stk | Benennung | Dimmensionen  | wird verwendet für |
| --- | --- | --- | --- |
| 4 | Distanzbolzen M2.5 | Männchen 12mm | Pi <> UPS |
| 4 | Distanzbolzen M2.5 | Männchen 25mm | UPS <> Motorplatte |
| 4 | Distanzbolzen M2.5 | Weibchen 10mm | Grundplatte <> Motorplatte |
| 4 | Distanzbolzen M2.5 | Männchen 5mm  | Pi <> Topplatte |

## 8. Zusammenbau Kopf

#### Kopf Schütteln

Pan turret assembly-1 Pan turret assembly-2

#### Nicken

Tilt turret assembly-1 Tilt turret assembly-2

#### kompletter Kopf

Pan + Tilt turret assembly-1 Pan + Tilt turret assembly-2

#### Kamera

Die Infrarot-Seitenteile müssen mit dem Kamerakopf elektrisch leitend verbunden sein. Auf die Polarität achten. Mit den langen Schrauben und Muttern klemmen, danach ins gedruckte Teil einbauen und noch einmal mit Muttern sichern. Oder so wie auf den Bildern. Wichtig ist, dass die IR-Seitenteile mit Spannung versorgt werden. <br>

Camera assembly-1 Camera assembly-2

[Zusätzliche Anleitung in Englisch](https://www.robot-maker.com/forum/topic/13101-pan-tilt-minus-hardware-documentation/)

## 9. Zusammenbau Greifer

Gripper assembly-1 Gripper assembly-2
Gripper assembly-3 Gripper assembly-4
Gripper assembly-5 Gripper assembly-6
Gripper assembly-7 Final assembly-1
Final assembly-2

[Zusätzliche Anleitung in Englisch](https://www.robot-maker.com/forum/topic/13108-minus-gripper-assembly/)

## 10. Finale Fertigstellung

Final assembly-3 Final assembly-4
Final assembly-5 Final assembly-6
Final assembly-7 Final assembly-8
Final assembly-9 Minus render-1

Alle Servohörner müssen satt sitzen und dürfen kein Spiel haben.

* Mikrofon an einem der USB Anschlüsse einstecken.
* LTE / 4G Stick in 90° Winkelstecker stecken und diesen in einen der USB Anschlüsse einstecken.
* Der Roboter sollte nun betriebsbereit sein.
* Steuere über die Vigibot-Website, überprüfe jeden Servoweg und stelle die Servohörner bei Bedarf neu ein.
* Stelle beide Infrarot-IR-LEDs auf die schwächste Beleuchtung ein, indem du den Helligkeitssensor/Fotowiderstand abdeckst, das kleine Potentiometer auf den IR-LED-Platinen drehst und mit einer Smartphone-Kamera beobachtest.

### 10.1 Aufkleber auf dem Roboter

labels_bottom stick_1
Stick 2

Um die Bedienung des Roboters durch die Nutzer zu vereinfachen, wird empfohlen, folgende Aufkleber zu drucken und anzubringen. Die mit ** Text ** geführten Ausdrücke müssen passend zu eurem Roboter angepasst werden. Die Schriftgrösse so anpassen, dass die Aufkleber Platz haben. Beim Hinweis zum LED-Farbcode des 4G Sticks muss auf den Typ des Sticks geachtet werden.

| Nr. | Benennung | Text  | Position am Roboter |
| --- | --- | --- | --- |
| 1 | Name | *Name: ** NAME ** botkins.ch [Nr. ** Roboternummer **]*| oben/unten auf dem Roboter |
| 2 | Hauptschalter | *Ein / Aus* | Beim Hauptschalter des Spannungsversorgungsmoduls (UPS) |
| 3 | Startvorgang | *Startvorgang dauert 30s* | oben/unten auf dem Roboter |
| 4 | Hinweis Betrieb | *Roboterli ist designt, um durchgehend eingesteckt und eingeschaltet zu sein.*  | oben/unten auf dem Roboter|
| 5 | Empfang 4G Stick | *2x Blau: Empfang ok, Rot + Blau: kein Empfang* | auf dem 4G Stick |
| 6 | Hinweis 4G Stick | *4G Stick für botkins.ch vigibot.com* | auf dem 4G Stick |
| 7* | Ladehinweis | *Roboter mit dem Netzteil laden, nicht am Raspberry* | in der Nähe der Ladebuchse |
| 8* | WLAN Konfig | *Zum Verbinden mit WLAN Robo einschalten und mit Netzwerk "Vigibot WiFi Config" verbinden* | oben/unten auf dem Roboter |

7* Je nach verbauter Spannungsversorgung (UPS) ist dieser Hinweis anders zu gestalten. Wichtig ist, dass der Robo nicht über den USB-Anschluss des Raspberry geladen wird. Am besten den richtigen Anschluss farblich kennzeichnen und ein Foto dem Begleitbrief beilegen.
8* Nur, wenn balena WLAN-Config installiert ist

## 11. Optionale Schritte

### apt repositories aktualisieren

<details>
<summary>[Diesen Abschnitt anzeigen]</summary>

Um Dinge installieren zu können, müssen die Quellen für `apt` aktualisiert werden, da die ursprünglichen Paketquellen nicht mehr verfügbar sind.

> ⚠️ Achtung: Während der Installation wird die bestehende WLAN-Verbindung getrennt.

* Verbinde den Roboter über **Ethernet** mit deinem lokalen Netzwerk.

* Öffne die [Vigibot Website](https://www.vigibot.com) und fahre mit dem Cursor auf das Roboter-Icon.
   * Notiere die **LAN-IP-Adresse** deines Roboters, die angezeigt wird, zB 192.168.1.90

* Verbindung per SSH herstellen. Je nach Betriebssystem:

  * **Windows:** Nutze z.B. [PuTTY](https://www.putty.org/)
  * **Android:** Nutze [Termius](https://play.google.com/store/apps/details?id=com.server.auditor.ssh.client) oder eine andere SSH-App.

* Win+R > „Powershell“ > Ausführen öffnet das Terminal
*	Gib im Fenster ein: ssh pi\@IP-ADRESSE (Ersetze die Adresse mit der Adresse des Pi, zB 192.168.1.146)
*	Das Terminal wird dich fragen, ob du sicher bist, eine Verbindung herstellen zu wollen. Schreibe „yes“ und bestätige
*	Verwende das Passwort, das du oben vergeben hast. Hast du robot.json nicht verändert, ist es „raspberry“.

1. raspi.list anpassen

```Shell
sudo nano /etc/apt/sources.list.d/raspi.list
```

Kommentiere alle vorhandenen Zeilen aus (mit # am Anfang der Zeile)
und füge folgende Zeilen ein:

```
deb http://legacy.raspbian.org/raspbian/ buster main contrib non-free rpi
deb http://archive.raspberrypi.org/debian buster main
```

Speichern (PuTTY):
Strg+O → Enter → Strg+X

1. sources.list anpassen

```
sudo nano /etc/apt/sources.list
```

Kommentiere hier ebenfalls alle vorhandenen Zeilen aus.

Speichern (PuTTY):
Strg+O → Enter → Strg+X

1. Paketlisten aktualisieren

```
sudo apt update
```

Danach sollte apt korrekt funktionieren.

</details>

### WLAN Unterstützung Einrichten

<details>
<summary>[Diesen Abschnitt anzeigen]</summary>

Mit diesem Abschnitt kannst du deinem Roboter ermöglichen, sich per WLAN mit deinem Netzwerk zu verbinden. Wir nutzen dazu das **balena** **`wifi-connect`-Tool**, das ein Captive-Portal auf dem Roboter startet.

1. Führe zuerst den obigen Abschnitt `apt repositories aktualisieren` durch, bevor du weiterfährst.

2. Mit SSH zum Roboter verbinden
```Shell
ssh pi@ROBOT_IP
```

3. balena wifi-connect installieren

```
bash <(curl -L https://github.com/balena-io/wifi-connect/raw/master/scripts/raspbian-install.sh)
```

4. start\_Vigibot\_WiFi\_Config.sh erstellen

```
nano ~/start_Vigibot_WiFi_Config.sh
```

Füge folgenden Inhalt ein:

```
#!/usr/bin/env bash

printf 'Warten, um der WLAN verbindung Zeit zu geben, sich zu verbinden\n'
sleep 25

# Prüfen, ob bereits eine WLAN-Verbindung besteht
iwgetid -r
if [ $? -eq 0 ]; then
    printf 'Skipping WiFi Connect\n'
else
    printf 'Starting WiFi Connect\n'
    /usr/local/sbin/wifi-connect --portal-ssid "Vigibot WiFi Config" --portal-passphrase "64robots"
fi

sleep infinity
```

PuTTY Speichern: Strg+O, Enter, Strg+X.

5. Datei ausführbar machen

```
chmod +x ~/start_Vigibot_WiFi_Config.sh
```

6. rc.local anpassen
   Damit das WLAN-Captive-Portal automatisch beim Booten startet:

```
sudo nano /etc/rc.local
```

Füge vor `exit 0` folgende Zeile ein:

```
/home/pi/start_Vigibot_WiFi_Config.sh &
```

Speichern PuTTY: Strg+O, Enter, Strg+X.

7. Roboter neu starten

```
sudo reboot
```

Nach dem Neustart startet der Roboter automatisch das Captive-Portal `Vigibot WiFi Config` mit dem Passwort `64robots`.

1. Verbinde dein Smartphone zum Access Point `Vigibot WiFi Config`. Es kann ca 60 Sekunden dauern, bis wifi-connect gestartet wird.
2. Öffne eine beliebige Website in einem Browser, das Captive-Portal wird dich automatisch zum Konfikurationsportal weiterleiten.
3. Dort kannst du das gewünschte Heim-WLAN-Netzwerk aus einer Liste auswählen, womit sich der Roboter dann verbindet.

</details>

## 12. Zusätzliche Bauanleitungen

* Weitere [Montageanleitungen](https://www.robot-maker.com/forum/topic/13063-vigibot-hardware-documentation/) in französischer Sprache
* Kurzes [Montagevideo](https://youtu.be/9Eja0gG4bhI) aus der Community
* [Vigibot FAQ](https://www.robot-maker.com/forum/topic/12787-vigibot-faq-en-fr/)

## 13. Funktionstest

Nun ist es Zeit für den finalen Check!
Teste die Funktionen des Roboters:

1. Roboter auf vigibot.com sichtbar mit korrektem Namen?
2. Alle Bedienelemente vorhanden? Wenn nicht > botkins Team fragen

   servo_assembly_4
4. Spannungsanzeige zuunterst ist vorhanden? Wenn nicht, botkins Team fragen

   servo_assembly_4
6. Steuerbefehle (vorwärts, rückwärts, links, rechts) funktionieren?
7. Alle Räder drehen?
8. Robo lässt sich präzise fahren, auch schnelles Drehen ist möglich?
9. Robo fällt beim abrupten Bremsen nicht vornüber?
10. Antriebsmotoren sind vor Staub und Zugriff geschützt?
11. Ruderhörner der Servos sind passgenau und spielfrei verbaut?
12. Kopf lässt sich drehen?
13. Kopf dreht symmetrisch in beide Richtungen? Wenn nicht > Servohorn lösen und in Ruhestellung einmitten
14. Nicken funktioniert?
15. Nicken symmetrisch in beide Richtungen? Wenn nicht > Servohorn lösen und in Ruhestellung einmitten
16. Der Greifer muss bis auf den Boden greifen können und sich komplett öffnen und schliessen lassen.
17. Der Greifer darf nicht „hängenbleiben“, was passieren kann, wenn die Schrauben zu weit/zu fest eingeschraubt sind. Dazu die Bewegungen ganz langsam durchführen.
18. Bei vollständigen Kopf- und Greiferbewegungen dürfen keine Kabel gezogen werden.
19. Verbinde dich mit Vigibot und stell die Kamera auf einen Text gerichtet scharf.
20. Schau mit dem Smartphone auf die "Augen", die IR-LEDs. Decke den runden Helligkeitssensor ab. Stelle die Helligkeit nun mit einem winzigen Schlitzschraubendreher auf das Minimum. Auf der anderen Seite wiederholen. Das verhindert übermässigen Akkuverbrauch.
21. Ist der Winkelstecker und der LTE/4G Stick und der Auffahrschutz montiert?
22. Teste den Roboter mit LTE/4G Stick, bei Dunkelheit, fahre und bewege Kopf oder Greifer bei niedrigem Akkustand (ca 3,3V – 3,5V), ob Abstürze auftreten.
23. Ist die Ladebuchse des Roboters zugänglich?
24. Lass den Akku des Roboters vollständig entladen. Die Servos können sich leicht bewegen, aber der Roboter sollte nicht von selbst fahren.
25. Lasse den Roboter eingeschaltet und schliesse bei vollständig entladenem Akku das Ladekabel an. Er sollte nicht in einer Boot-Schleife hängenbleiben.
26. Lade den Roboter Komplett auf (aufladen dauert bis zu 10h eingeschaltet, 4h ausgeschaltet). Die Spannung sollte beim Ausgestecken von 4,1–4,2V nicht unter 3,9V fallen. Sonst ist der Widerstand zum Akku zu gross, dazu evtl die Akkukabel direkt am UPS anlöten.
27. Mirofon testen
28. Sind die Aufkleber angebracht?

</details>

## Troubleshooting

<details open>
<summary>[Diesen Abschnitt verbergen]</summary>

Wenn du anhand der folgenden Tabelle keine Lösung findest, frage im Vigibot-Discord-Server (Tag @firened) oder in der Botkins Maker Signal-Gruppe nach.

| Problem | Mögliche Ursachen | Lösung | wichtig für |
| --- | --- | --- | --- |
| Der Roboter trennt sich sporadisch (alle paar Stunden oder Minuten) | (1) Schwache Batterie (2) Schlechter 4G-Empfang | (1) Aufladen (2) Einen anderen Standort ausprobieren | Nutzer |
| Der Roboter blinkt (visuell) und klickt (akustisch) alle paar Sekunden oder mehrmals pro Sekunde | Schwache Batterie | Roboter ausschalten und mehrere Stunden lang aufladen | Nutzer |
| Der Roboter trennt alle 5 Sekunden die Verbindung | Fehlerhafte Konfiguration von Vigibot | Bitten Sie Vigibot oder Botkins, die Online-Konfiguration der Roboter zu überprüfen | Nutzer |
| Der Akku ist nach \~5 Tagen leer, obwohl das Gerät ausgeschaltet ist | Einige Teile (Servos, Motortreiber) werden auch im ausgeschalteten Zustand mit Strom versorgt und entladen die Batterie | kann leider nicht geändert werden | Nutzer |
| Das Video stottert, das Fahren wird unterbrochen, alle paar Sekunden erscheinen rote Balken auf der Website | Schlechter 4G-Empfang, zu geringe 4G-Bandbreite | Wählen Sie die Ansicht mit niedriger Bandbreite, probieren Sie einen anderen Standort aus und stellen Sie sicher, dass die mobile Datenübertragungsgeschwindigkeit mindestens „bis zu 50 Mbit/s“ beträgt | Nutzer |
| Robo erscheint nicht, im vigibot.com, oder nur kurz | Ist der 4G/LTE Stick eingesteckt, aber es besteht keine Verbindung, wird nur auf WLAN umgeschaltet, wenn der Stick entfernt wird | Stick ausstecken, wenn über WLAN verbunden werden soll | Nutzer |
| Während der Montage ist der Roboter nach einem Neustart für einige Sekunden online und verschwindet dann | Keine 4G-Verbindung/Empfang | Ziehen Sie den 4G-Stick ab und versuchen Sie es mit WLAN oder Ethernet | Maker |
| Der Roboter lässt sich über ssh nicht verbinden, obwohl die IP-Adresse bekannnt ist | Firewall oder VPN blockt | Firewall oder VPN temporär ausschalten | Maker |
| ssh meldet trotz korrekter IP Adresse "  @@@ WARNING: REMOTE HOST IDENTIFICATION HAS CHANGED! @@@ ..." | Neues Image, alter Key | ssh-keygen -R 192.168.1.200 im Terminal eingeben und Enter, alter Key gelöscht. Erneut einloggen | Maker |
| Verbindung per ssh nicht möglich nach Aufspielen von neuem Image | Image hat Standardpasswort mitgegeben | SD Card in PC > boot > robot.json Name und Passwort vergeben ODER Standardpasswort "raspberry" verwenden, um ssh zu starten | Maker |
| Spannung wird im vigibot Interface nicht korrekt angezeigt (2.5V) | Grund liegt je nach UPS am Pin, auf dem die Info an den PI gelangt. |Bsp: sudo nano /usr/local/vigiclient/sys.json > "INA219ADDRESS": 66 | Maker |

|                                                                                                             |                                                                                                                         |                                                                                                                                                                                                          |             |

</details>

## Credits

* Original Partlist: Vigibot
* Assembly Renders: Narayan1986
* Partlist Modifications: Botkins Charity Project
* Assembly Guide: Botkins Charity Project (unless otherwise noted)

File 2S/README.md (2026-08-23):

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

# Minus-Type 2S Robot für Botkins

## Inhalt

<details open>
<summary>[Diesen Abschnitt verbergen]</summary>

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

</details>

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

## 1.1 Das Botkins Charity Project
Erfahre mehr über das Botkins Charity Project:

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

Botkins S2

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

[⬆️ Zurück zum Inhaltsverzeichnis](#inhalt)

# 2. Voraussetzungen

Du benötigst:

* Komplettkit Minus-Type S2 [robot-maker.com](https://www.robot-maker.com/shop/kits-robots/284-kit-minus-2s-284.html) oder bestellbar bei uns an Adresse
* Internetzugang (SIM-Karte mit mobilen Daten, WLAN oder Ethernet-LAN), PC.
* Ein 3D-Drucker ist derzeit nicht erforderlich. Wenn du die 3D-Teile selbst drucken möchtest, werden M2- und M2,5-Schrauben und Muttern, die in der entsprechenden Botkins-Teileliste aufgeführt sind, benötigt. Du findest sie in der Teileliste in jedem der 3D-gedruckten Sektionen.
* Werkzeuge: Schraubenzieher, verstellbarer Schraubenschlüssel/Gabelschlüssel, Pinzette, Klebeband, Sekundenkleber
* SD-Cardreader für microSD

[⬆️ Zurück zum Inhaltsverzeichnis](#inhalt)

# 3. Teileliste

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

## 3.1 Hauptteile

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

[⬆️ Zurück zum Inhaltsverzeichnis](#inhalt)
</details>

# 4. Minus Type 2S Zusammenbau

## 4.1 Software Installieren

pi_cam<br>

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

Falls du auf den Pi zugreifen willst:

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

LTE/4G Mobile Data Stick:

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

[⬆️ Zurück zum Inhaltsverzeichnis](#inhalt)

## 4.2 Vigibot Online Konfiguration

### Konfiguration der Fernsteuerung über Vigibot

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

<details>
<summary>[SHOW CODE BLOCK]</summary>

```JSON
{
  "BUTTONS": [
    {
      "ICON0": "switch0",
      "ICON1": "switch1",
      "TEXT": "Power Enable",
      "ACTION": "Switch0",
      "SPECIAL": "i0"
    },
    {
      "ICON0": "projecteur0",
      "ICON1": "projecteur1",
      "TEXT": "LED spotlights",
      "ACTION": "Switch1",
      "SPECIAL": "i1"
    },
    {
      "ICON0": "vide",
      "ICON1": "",
      "TEXT": "",
      "ACTION": "",
      "SPECIAL": ""
    },
    {
      "ICON0": "avancer",
      "ICON1": "",
      "TEXT": "Forward",
      "ACTION": "IncrementForward",
      "SPECIAL": "yp"
    },
    {
      "ICON0": "vide",
      "ICON1": "",
      "TEXT": "",
      "ACTION": "",
      "SPECIAL": ""
    },
    {
      "ICON0": "suivant",
      "ICON1": "",
      "TEXT": "Next tool",
      "ACTION": "NextTool",
      "SPECIAL": ""
    },
    {
      "ICON0": "sirene0",
      "ICON1": "sirene1",
      "TEXT": "Buzzer",
      "ACTION": "Switch2",
      "SPECIAL": "i2"
    },
    {
      "ICON0": "lumicont0",
      "ICON1": "lumicont1",
      "TEXT": "Maximize the brightness and contrast",
      "ACTION": "Switch3",
      "SPECIAL": "i3"
    },
    {
      "ICON0": "gauche",
      "ICON1": "",
      "TEXT": "Left",
      "ACTION": "IncrementTurnLeft",
      "SPECIAL": "zn"
    },
    {
      "ICON0": "stopper",
      "ICON1": "",
      "TEXT": "Click to stop or drag to drive",
      "ACTION": "Brake",
      "SPECIAL": "st"
    },
    {
      "ICON0": "droite",
      "ICON1": "",
      "TEXT": "Right",
      "ACTION": "IncrementTurnRight",
      "SPECIAL": "zp"
    },
    {
      "ICON0": "centrer",
      "ICON1": "",
      "TEXT": "Reset tools",
      "ACTION": "ResetTools",
      "SPECIAL": ""
    },
    {
      "ICON0": "gyrophare0",
      "ICON1": "gyrophare1",
      "TEXT": "Warning light mode",
      "ACTION": "Switch4",
      "SPECIAL": "i4"
    },
    {
      "ICON0": "vide",
      "ICON1": "",
      "TEXT": "",
      "ACTION": "",
      "SPECIAL": ""
    },
    {
      "ICON0": "vide",
      "ICON1": "",
      "TEXT": "",
      "ACTION": "",
      "SPECIAL": ""
    },
    {
      "ICON0": "reculer",
      "ICON1": "",
      "TEXT": "Backward",
      "ACTION": "IncrementBackward",
      "SPECIAL": "yn"
    },
    {
      "ICON0": "capture",
      "ICON1": "",
      "TEXT": "Capture the last seconds of video",
      "ACTION": "",
      "SPECIAL": "capture"
    },
    {
      "ICON0": "precedent",
      "ICON1": "",
      "TEXT": "Previous tool",
      "ACTION": "PreviousTool",
      "SPECIAL": ""
    },
    {
      "ICON0": "vide",
      "ICON1": "",
      "TEXT": "",
      "ACTION": "",
      "SPECIAL": ""
    },
    {
      "ICON0": "vide",
      "ICON1": "",
      "TEXT": "",
      "ACTION": "",
      "SPECIAL": ""
    },
    {
      "ICON0": "lock0",
      "ICON1": "lock1",
      "TEXT": "Unlink remote control and video",
      "ACTION": "",
      "SPECIAL": "switchlock"
    },
    {
      "ICON0": "osd0",
      "ICON1": "osd1",
      "TEXT": "Toggle OSD",
      "ACTION": "",
      "SPECIAL": "switchosd"
    },
    {
      "ICON0": "vide",
      "ICON1": "",
      "TEXT": "",
      "ACTION": "",
      "SPECIAL": ""
    },
    {
      "ICON0": "dodo",
      "ICON1": "",
      "TEXT": "Put on standby",
      "ACTION": "Sleep",
      "SPECIAL": ""
    },
    {
      "ICON0": "vide",
      "ICON1": "",
      "TEXT": "",
      "ACTION": "",
      "SPECIAL": ""
    },
    {
      "ICON0": "vide",
      "ICON1": "",
      "TEXT": "",
      "ACTION": "",
      "SPECIAL": ""
    },
    {
      "ICON0": "vide",
      "ICON1": "",
      "TEXT": "",
      "ACTION": "",
      "SPECIAL": ""
    },
    {
      "ICON0": "exit",
      "ICON1": "",
      "TEXT": "Restart the client process",
      "ACTION": "ExitRobot",
      "SPECIAL": "confirm"
    },
    {
      "ICON0": "reboot",
      "ICON1": "",
      "TEXT": "Reboot the system",
      "ACTION": "RebootRobot",
      "SPECIAL": "confirm"
    },
    {
      "ICON0": "poweroff",
      "ICON1": "",
      "TEXT": "Power off the system",
      "ACTION": "PowerOffRobot",
      "SPECIAL": "confirm"
    }
  ],
  "COMMANDS": [
    {
      "NAME": "Turret control",
      "CAMERA": 0,
      "MIXING": 0,
      "GAINX": 80,
      "GAINY": 80
    },
    {
      "NAME": "Gripper control",
      "CAMERA": 0,
      "MIXING": 1,
      "GAINX": 80,
      "GAINY": 80
    },
    {
      "NAME": "250 Kbps - Camera control",
      "CAMERA": 1,
      "MIXING": 0,
      "GAINX": 80,
      "GAINY": 80
    },
    {
      "NAME": "250 Kbps - Gripper control",
      "CAMERA": 1,
      "MIXING": 1,
      "GAINX": 80,
      "GAINY": 80
    }
  ],
  "TX": {
    "COMMANDS16": [
      {
        "NAME": "Turret X",
        "INIT": 0,
        "SCALEMIN": -180,
        "SCALEMAX": 180,
        "MIN": -90,
        "MAX": 90,
        "CLAMPMIN": -20,
        "CLAMPMAX": 20,
        "SIGNED": true,
        "NBDIGITS": 2,
        "UNIT": "°"
      },
      {
        "NAME": "Turret Y",
        "INIT": 8,
        "SCALEMIN": -180,
        "SCALEMAX": 180,
        "MIN": -55,
        "MAX": 55,
        "CLAMPMIN": -40,
        "CLAMPMAX": 20,
        "SIGNED": true,
        "NBDIGITS": 2,
        "UNIT": "°"
      },
      {
        "NAME": "Gripper X",
        "INIT": 0,
        "SCALEMIN": -180,
        "SCALEMAX": 180,
        "MIN": -35,
        "MAX": 70,
        "CLAMPMIN": -35,
        "CLAMPMAX": 65,
        "SIGNED": true,
        "NBDIGITS": 2,
        "UNIT": "°"
      },
      {
        "NAME": "Gripper Y",
        "INIT": 20,
        "SCALEMIN": -180,
        "SCALEMAX": 180,
        "MIN": -40,
        "MAX": 80,
        "CLAMPMIN": 0,
        "CLAMPMAX": 45,
        "SIGNED": true,
        "NBDIGITS": 2,
        "UNIT": "°"
      }
    ],
    "COMMANDS1": [
      {
        "NAME": "Power Enable",
        "INIT": 1
      },
      {
        "NAME": "LED spotlights",
        "INIT": 1
      },
      {
        "NAME": "Buzzer",
        "INIT": 0
      },
      {
        "NAME": "Brightness boost",
        "INIT": 0
      },
      {
        "NAME": "Switch 4",
        "INIT": 0
      },
      {
        "NAME": "Switch 5",
        "INIT": 0
      },
      {
        "NAME": "Switch 6",
        "INIT": 0
      },
      {
        "NAME": "Switch 7",
        "INIT": 0
      }
    ]
  },
  "RX": {
    "VALUES16": [
      {
        "NAME": "Voltage",
        "INIT": 3,
        "SCALEMIN": 6,
        "SCALEMAX": 9,
        "MIN": 6,
        "MAX": 9,
        "SIGNED": false,
        "NBDIGITS": 2,
        "UNIT": " V"
      },
      {
        "NAME": "Current",
        "INIT": 0,
        "SCALEMIN": -5,
        "SCALEMAX": 5,
        "MIN": -5,
        "MAX": 5,
        "SIGNED": true,
        "NBDIGITS": 2,
        "UNIT": " A"
      }
    ]
  }
}
```

</details>

### Hardware Konfiguration

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

<details>
<summary>[SHOW CODE BLOCK]</summary>

*Sicherstellen, dass es die  2S Config ist!*

```JSON
{
  "CAMERAS": [
    {
      "TYPE": "",
      "SOURCE": 0,
      "WIDTH": 640,
      "HEIGHT": 480,
      "FPS": 30,
      "BITRATE": 1500000,
      "ROTATE": 180,
      "BRIGHTNESS": 50,
      "CONTRAST": -5,
      "BRIGHTNESSBOOST": 80,
      "CONTRASTBOOST": 100
    },
    {
      "TYPE": "",
      "SOURCE": 0,
      "WIDTH": 640,
      "HEIGHT": 480,
      "FPS": 30,
      "BITRATE": 250000,
      "ROTATE": 180,
      "BRIGHTNESS": 50,
      "CONTRAST": -5,
      "BRIGHTNESSBOOST": 80,
      "CONTRASTBOOST": 100
    }
  ],
  "OUTPUTS": [
    {
      "NAME": "Turret pan",
      "TYPE": "Servos",
      "ADRESSE": -1,
      "GPIOS": [
        5
      ],
      "SLEEPMODES": [
        "Floating"
      ],
      "INS": [
        -135,
        135
      ],
      "OUTS": [
        500,
        2400
      ],
      "BACKSLASH": 0,
      "COMMANDS16": [
        0
      ],
      "GAINS16": [
        -1
      ],
      "COMMANDS8": [],
      "GAINS8": [],
      "COMMANDS1": [],
      "GAINS1": []
    },
    {
      "NAME": "Turret tilt",
      "TYPE": "Servos",
      "ADRESSE": -1,
      "GPIOS": [
        6
      ],
      "SLEEPMODES": [
        "Floating"
      ],
      "INS": [
        -90,
        90
      ],
      "OUTS": [
        500,
        2500
      ],
      "BACKSLASH": 0,
      "COMMANDS16": [
        1
      ],
      "GAINS16": [
        -1
      ],
      "COMMANDS8": [],
      "GAINS8": [],
      "COMMANDS1": [],
      "GAINS1": []
    },
    {
      "NAME": "Gripper claw",
      "TYPE": "Servos",
      "ADRESSE": -1,
      "GPIOS": [
        7
      ],
      "SLEEPMODES": [
        "Floating"
      ],
      "INS": [
        -90,
        90
      ],
      "OUTS": [
        500,
        2500
      ],
      "BACKSLASH": 0,
      "COMMANDS16": [
        2
      ],
      "GAINS16": [
        -1
      ],
      "COMMANDS8": [],
      "GAINS8": [],
      "COMMANDS1": [],
      "GAINS1": []
    },
    {
      "NAME": "Gripper tilt",
      "TYPE": "Servos",
      "ADRESSE": -1,
      "GPIOS": [
        8
      ],
      "SLEEPMODES": [
        "Floating"
      ],
      "INS": [
        -90,
        90
      ],
      "OUTS": [
        500,
        2500
      ],
      "BACKSLASH": 0,
      "COMMANDS16": [
        3
      ],
      "GAINS16": [
        -1
      ],
      "COMMANDS8": [],
      "GAINS8": [],
      "COMMANDS1": [],
      "GAINS1": []
    },
    {
      "NAME": "Front left wheel",
      "TYPE": "PwmPwm",
      "ADRESSE": -1,
      "GPIOS": [
        22,
        23
      ],
      "SLEEPMODES": [
        "Low",
        "Low"
      ],
      "INS": [
        -100,
        -1,
        1,
        100
      ],
      "OUTS": [
        -100,
        -1,
        1,
        100
      ],
      "BACKSLASH": 0,
      "COMMANDS16": [],
      "GAINS16": [],
      "COMMANDS8": [
        0,
        1,
        2
      ],
      "GAINS8": [
        1,
        1,
        -1
      ],
      "COMMANDS1": [],
      "GAINS1": []
    },
    {
      "NAME": "Front right wheel",
      "TYPE": "PwmPwm",
      "ADRESSE": -1,
      "GPIOS": [
        24,
        25
      ],
      "SLEEPMODES": [
        "Low",
        "Low"
      ],
      "INS": [
        -100,
        -1,
        1,
        100
      ],
      "OUTS": [
        -100,
        -1,
        1,
        100
      ],
      "BACKSLASH": 0,
      "COMMANDS16": [],
      "GAINS16": [],
      "COMMANDS8": [
        0,
        1,
        2
      ],
      "GAINS8": [
        1,
        -1,
        -1
      ],
      "COMMANDS1": [],
      "GAINS1": []
    },
    {
      "NAME": "Rear left wheel",
      "TYPE": "PwmPwm",
      "ADRESSE": -1,
      "GPIOS": [
        16,
        17
      ],
      "SLEEPMODES": [
        "Low",
        "Low"
      ],
      "INS": [
        -100,
        -1,
        1,
        100
      ],
      "OUTS": [
        -100,
        -1,
        1,
        100
      ],
      "BACKSLASH": 0,
      "COMMANDS16": [],
      "GAINS16": [],
      "COMMANDS8": [
        0,
        1,
        2
      ],
      "GAINS8": [
        -1,
        1,
        -1
      ],
      "COMMANDS1": [],
      "GAINS1": []
    },
    {
      "NAME": "Rear right wheel",
      "TYPE": "PwmPwm",
      "ADRESSE": -1,
      "GPIOS": [
        26,
        27
      ],
      "SLEEPMODES": [
        "Low",
        "Low"
      ],
      "INS": [
        -100,
        -1,
        1,
        100
      ],
      "OUTS": [
        -100,
        -1,
        1,
        100
      ],
      "BACKSLASH": 0,
      "COMMANDS16": [],
      "GAINS16": [],
      "COMMANDS8": [
        0,
        1,
        2
      ],
      "GAINS8": [
        -1,
        -1,
        -1
      ],
      "COMMANDS1": [],
      "GAINS1": []
    },
    {
      "NAME": "Power Enable",
      "TYPE": "Gpios",
      "ADRESSE": -1,
      "GPIOS": [
        13
      ],
      "SLEEPMODES": [
        "Low"
      ],
      "INS": [
        0,
        1
      ],
      "OUTS": [
        0,
        1
      ],
      "BACKSLASH": 0,
      "COMMANDS16": [],
      "GAINS16": [],
      "COMMANDS8": [],
      "GAINS8": [],
      "COMMANDS1": [
        0
      ],
      "GAINS1": [
        1
      ]
    },
    {
      "NAME": "LED spotlights",
      "TYPE": "Gpios",
      "ADRESSE": -1,
      "GPIOS": [
        9
      ],
      "SLEEPMODES": [
        "Low"
      ],
      "INS": [
        0,
        1
      ],
      "OUTS": [
        0,
        1
      ],
      "BACKSLASH": 0,
      "COMMANDS16": [],
      "GAINS16": [],
      "COMMANDS8": [],
      "GAINS8": [],
      "COMMANDS1": [
        1
      ],
      "GAINS1": [
        1
      ]
    },
    {
      "NAME": "Buzzer",
      "TYPE": "Pwms",
      "ADRESSE": -1,
      "GPIOS": [
        4
      ],
      "SLEEPMODES": [
        "None"
      ],
      "INS": [
        0,
        1
      ],
      "OUTS": [
        0,
        80
      ],
      "BACKSLASH": 0,
      "COMMANDS16": [],
      "GAINS16": [],
      "COMMANDS8": [],
      "GAINS8": [],
      "COMMANDS1": [
        2
      ],
      "GAINS1": [
        1
      ]
    },
    {
      "NAME": "Maximize the brightness and contrast",
      "TYPE": "Gpios",
      "ADRESSE": -1,
      "GPIOS": [
        1
      ],
      "SLEEPMODES": [
        "None"
      ],
      "INS": [
        0,
        1
      ],
      "OUTS": [
        0,
        1
      ],
      "BACKSLASH": 0,
      "COMMANDS16": [],
      "GAINS16": [],
      "COMMANDS8": [],
      "GAINS8": [],
      "COMMANDS1": [
        3
      ],
      "GAINS1": [
        1
      ]
    },
    {
      "NAME": "Switch 4",
      "TYPE": "Servos",
      "ADRESSE": -1,
      "GPIOS": [
        18
      ],
      "SLEEPMODES": [
        "None"
      ],
      "INS": [
        0,
        1
      ],
      "OUTS": [
        1000,
        2000
      ],
      "BACKSLASH": 0,
      "COMMANDS16": [],
      "GAINS16": [],
      "COMMANDS8": [],
      "GAINS8": [],
      "COMMANDS1": [
        4
      ],
      "GAINS1": [
        1
      ]
    },
    {
      "NAME": "Switch 5",
      "TYPE": "Gpios",
      "ADRESSE": -1,
      "GPIOS": [
        19
      ],
      "SLEEPMODES": [
        "None"
      ],
      "INS": [
        0,
        1
      ],
      "OUTS": [
        0,
        1
      ],
      "BACKSLASH": 0,
      "COMMANDS16": [],
      "GAINS16": [],
      "COMMANDS8": [],
      "GAINS8": [],
      "COMMANDS1": [
        5
      ],
      "GAINS1": [
        1
      ]
    },
    {
      "NAME": "Switch 6",
      "TYPE": "Gpios",
      "ADRESSE": -1,
      "GPIOS": [
        20
      ],
      "SLEEPMODES": [
        "None"
      ],
      "INS": [
        0,
        1
      ],
      "OUTS": [
        0,
        1
      ],
      "BACKSLASH": 0,
      "COMMANDS16": [],
      "GAINS16": [],
      "COMMANDS8": [],
      "GAINS8": [],
      "COMMANDS1": [
        6
      ],
      "GAINS1": [
        1
      ]
    },
    {
      "NAME": "Switch 7",
      "TYPE": "Gpios",
      "ADRESSE": -1,
      "GPIOS": [
        21
      ],
      "SLEEPMODES": [
        "None"
      ],
      "INS": [
        0,
        1
      ],
      "OUTS": [
        0,
        1
      ],
      "BACKSLASH": 0,
      "COMMANDS16": [],
      "GAINS16": [],
      "COMMANDS8": [],
      "GAINS8": [],
      "COMMANDS1": [
        7
      ],
      "GAINS1": [
        1
      ]
    }
  ],
  "COMMANDS8": [
    {
      "RAMPUP": 0,
      "RAMPDOWN": 0,
      "RAMPINIT": 0,
      "FAILSAFE": true,
      "SLEEP": true
    },
    {
      "RAMPUP": 15,
      "RAMPDOWN": 15,
      "RAMPINIT": 15,
      "FAILSAFE": true,
      "SLEEP": true
    },
    {
      "RAMPUP": 15,
      "RAMPDOWN": 15,
      "RAMPINIT": 15,
      "FAILSAFE": true,
      "SLEEP": true
    }
  ],
  "PWMFREQUENCY": 1000
}
```
[⬆️ Zurück zum Inhaltsverzeichnis](#inhalt)
</details>

## 4.3 Zusammenbau Motorplatte

Benötigtes Material aus dem Kit:

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

Einlegen der vier Motoren in die Vertiefungen in der Basis, Pins gegen oben

Übersicht Motorplatte <br>

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

Übersicht Motorplatte <br>

Die Räder können aufgesteckt, der Akku eingesteckt und im Batteriehalter platziert werden.

Übersicht Motorplatte <br>

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

Bewegungen Kopf und Greifer Steckerbelegung<br>

[⬆️ Zurück zum Inhaltsverzeichnis](#inhalt)

## 4.4 Zusammenbau Body

Benötigtes Material aus dem Kit:

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

*Optinale Teile

body complete

Hinweis: Das Drehlicht fehlt auf dem Bild

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

Speaker Assembly Top Speaker Assembly Bottom

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

Pin Cover Top Print

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

Camera Cable

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

Die microSD Card in den Karten-Slot auf der vorderen kurzen Seite des Pi einstecken.

Camera Signal Cable

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

Pi Assembly

Verbinderleiste auf die Stiftleister des Pi stecken

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

Kompletter Body

Mikrofon an einem der USB Anschlüsse einstecken

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

## 4.5 Roboter mit dem WLAN verbinden

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

Balena Startseite

Nun kannst du dich auf Vigibot mit dem Account des Roboters einloggen und herumfahren.

Hier die Erklärung der Standardbedienelemente:

Vigibot Bedienelemente

[⬆️ Zurück zum Inhaltsverzeichnis](#inhalt)

## 4.6 Zusammenbau Greifer und Kopf

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

Übersicht Greiferteile

Benötigtes Material aus dem Kit:

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

Kamera auf Print 

Nun Kamera und IR-LED Print mit den vier Schrauben am gedruckten Kopf befestigen.

Kamera an Kopf befestigen 

### Nicken

Servo von hinten ins gedruckte Kopfteil montieren und von der Seite mit zwei M2x14 Schrauben befestigen

Servo in Kopf 

### Kopf Schütteln

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

Teile vorbereiten 

### Kompletter Kopf

Druckteil inkl. Servo am Kopf befestigen und von beiden Seiten mit einer Schraube fixieren.

Kopf komplett 

### Greifer zusammenbauen

Servohorn einseitig in Greifarm links einbauen. 

Greifer zusammenbauen
Das Servokabel durch das Druckteil fädeln wie im Bild.

Greifer zusammenbauen

Die beiden Greifarme platzieren und mit den M2x12 Schrauben befestigen. Auf symmetrische Montage der Greifarme achten.

Servo mit 2x M2x14 am Halter Greifer befestigen.

Greifer zusammenbauen

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

Greifer zusammenbauen

### Kopf und Greifer an Halter bauen

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

Greifer zusammenbauen

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

Kopf und Greifer

[⬆️ Zurück zum Inhaltsverzeichnis](#inhalt)

## 4.7 Finale Fertigstellung

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

LTE / 4G Stick in 90° Winkelstecker stecken.
Der Roboter sollte nun betriebsbereit sein.

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

### Aufkleber auf dem Roboter

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

[⬆️ Zurück zum Inhaltsverzeichnis](#inhalt)

## 4.8 Optionale Schritte

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

### apt repositories aktualisieren

<details close>
<summary>[Diesen Abschnitt anzeigen]</summary>

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

1. raspi.list anpassen

```Shell
sudo nano /etc/apt/sources.list.d/raspi.list
```

Kommentiere alle vorhandenen Zeilen aus (mit # am Anfang der Zeile)
und füge folgende Zeilen ein:

```
deb http://legacy.raspbian.org/raspbian/ buster main contrib non-free rpi
deb http://archive.raspberrypi.org/debian buster main
```

Speichern (PuTTY):
Strg+O → Enter → Strg+X

1. sources.list anpassen

```
sudo nano /etc/apt/sources.list
```

Kommentiere hier ebenfalls alle vorhandenen Zeilen aus.

Speichern (PuTTY):
Strg+O → Enter → Strg+X

1. Paketlisten aktualisieren

```
sudo apt update
```

Danach sollte apt korrekt funktionieren.

</details>

### WLAN Unterstützung Einrichten

<details close>
<summary>[Diesen Abschnitt anzeigen]</summary>

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

Führe zuerst den obigen Abschnitt `apt repositories aktualisieren` durch, bevor du weiterfährst.

> ⚠️ Achtung: Während der Installation wird die bestehende WLAN-Verbindung getrennt.

1. Verbinde den Roboter über **Ethernet** mit deinem lokalen Netzwerk.

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

3. Verbindung per SSH herstellen. Je nach Betriebssystem:

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

Verbinde dich zu der notierten **IP-Adresse** des Roboters als Benutzer `pi` mit standart Passwort `raspberry`.

```Shell
ssh pi@ROBOT_IP
```

1. balena wifi-connect installieren

```
bash <(curl -L https://github.com/balena-io/wifi-connect/raw/master/scripts/raspbian-install.sh)
```

1. start\_BotkinsAP.sh erstellen

```
nano ~/start_BotkinsAP.sh
```

Füge folgenden Inhalt ein:

```
#!/usr/bin/env bash

printf 'Warten, um der WLAN verbindung Zeit zu geben, sich zu verbinden\n'
sleep 25

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

sleep infinity
```

PuTTY Speichern: Strg+O, Enter, Strg+X.

1. Datei ausführbar machen

```
chmod +x ~/start_BotkinsAP.sh
```

1. rc.local anpassen
   Damit das WLAN-Captive-Portal automatisch beim Booten startet:

```
sudo nano /etc/rc.local
```

Füge vor `exit 0` folgende Zeile ein:

```
/home/pi/start_BotkinsAP.sh &
```

Speichern PuTTY: Strg+O, Enter, Strg+X.

1. Roboter neu starten

```
sudo reboot
```

Nach dem Neustart startet der Roboter automatisch das Captive-Portal `BotkinsAP` mit dem Passwort `03Sessel`.

Verbinde dein Smartphone zum Access Point `BotkinsAP`.

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

[⬆️ Zurück zum Inhaltsverzeichnis](#inhalt)

</details>

## 4.9 Funktionstest

Nun ist es Zeit für den finalen Check!
Teste die Funktionen des Roboters:

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

[⬆️ Zurück zum Inhaltsverzeichnis](#inhalt)

# 5. Troubleshooting

<details open>
<summary>[Diesen Abschnitt verbergen]</summary>

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

</details>

# 6. Credits

* Original Partlist: Vigibot
* Partlist Modifications: Botkins Charity Project
* Assembly Guide: Botkins Charity Project (unless otherwise noted)

[⬆️ Zurück zum Inhaltsverzeichnis](#inhalt)

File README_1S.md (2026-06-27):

# Minus-Type 1S Vigibot Robot für Botkins

## Inhalt

<details open>
<summary>[Diesen Abschnitt verbergen]</summary>

* [Generelle Info](#generelle-info)
* [Voraussetzungen](#voraussetzungen)
* [Teileliste](#teileliste)
* [Minus-Type Zusammenbau](#minus-type-zusammenbau)
  * [1. Software Installieren](#1-software-installieren)
  * [2. Vigibot Online Konfiguration](#2-vigibot-online-konfiguration)
  * [3. UPS Solder Bridge](#3-ups-solder-bridge)
  * [4. Servostecker teilen](#4-servostecker-teilen)
  * [5. Spannungsversorgung](#5-spannungsversorgung)
  * [6. Signalleitungen verbinden](#6-signalleitungen-verbinden)
  * [7. Zusammenbau Motorplatte](#7-zusammenbau-motorplatte)
  * [8. Zusammenbau Kopf](#8-zusammenbau-kopf)
  * [9. Zusammenbau Greifer](#9-zusammenbau-greifer)
  * [10. Finale Fertigstellung](#10-finale-fertigstellung)
  * [11. Optionale Schritte](#11-optionale-schritte)
  * [12. Zusätzliche Bauanleitungen](#12-zusätzliche-bauanleitungen)
  * [13. Funktionstest](#13-funktionstest)
* [Troubleshooting](#troubleshooting)
* [Credits](#credits)

</details>

## Stand 2026-06-20

Das vigiUPSv3 ist nun verfügbar. Wir sind dabei die Updates von der upstream repo in diese Botkins Teileliste zu übernehmen.

## Stand 2026-02-13

Das UPS Bauteil ist aufgrund der mehreren neu gestarteten Roboterbauten im robot-maker Store ausverkauft.
Es gibt eine funktionierende Alternative, das «Waveshare UPS hat (D)» UPS, aber dies benötigt Modifikationen, sodass wir empfehlen auf das VigiUPSv3 zu warten, welches innert Monaten verfügbar sein sollte. Gib uns bescheid und wir schreiben dir sobald es verfügbar ist.

## Generelle Info

<details open>
<summary>[Diesen Abschnitt verbergen]</summary>

Dieser Leitfaden behandelt den Botkins V2. Weitere Verbesserungen sind in Arbeit und werden bald publiziert. Es ist geplant, ein komplettes Kit für Maker anzubieten. Es gibt aber keine Hürde oder Nachteil, einen Bot nach dieser Anleitung zu bauen. Die Funktionalität für die Patienten wird die selbe bleiben.

Erfahre mehr über das Botkins Charity Project:

* [botkins.ch](https://botkins.ch)&#x20;
* [Hackaday Page](https://hackaday.io/project/180558-botkins-charity-project)

Erfahre mehr über Vigibot:
Das französische Roboter-Projekt, wessen Software und Hardware Design Botkins benutzt.

* [Robot Maker Post](https://www.robot-maker.com/forum/topic/13010-what-is-vigibot-quest-ce-que-vigibot/)
* [Drive a robot Vigibot.com](https://www.vigibot.com/)

Als Basis dient die Standard Vigibot Minus-Type Version (siehe Bild, ein reines Botkin Bild folgt). Botkins ist zusätlich mit einem LTE/4G Stick ausgerüstet und kommt ohne Seitenarme aus.



* Wenn du für Botkins einen Roboter bauen möchtest, melde dich bei uns und wir senden dir die nötigen Informationen und den Zugang zu Resourcen.
* Als Maker kannst du die Farbe der 3D-gedruckten Teile selber wählen, sie ist nicht vorgegeben.
* Der Bau des ersten Roboters kann etwa 10 Stunden dauern, möglicherweise auch länger. Nach etwas Übung dauert der Bau etwa 3 Stunden pro Roboter.
* Einige Teile von Aliexpress können bis zu 5 Wochen fúr die Lieferung benötigen. Derzeit (2026) schlägt die Einstellung der Zahlungsmethode auf PayPal fehl, mit der Meldung "Sorry, some items are not available", bezahlen per Kreditkare funktioniert. Wähle [E-Mail order updates](https://www.aliexpress.com/p/edm-setting/index.html) vor dem Checkout ab, sonst bekommst du pro Bestellposition 3-5 Mails.

### Voraussetzungen

Du benötigst:

* Lötkolben (für die 4 Motoren und UPS-Brücke). (Wenn du nicht löten möchtest, kann vielleicht ein anderer Maker die Teile für löten).
* Internetzugang (SIM-Karte mit mobilen Daten, WLAN oder Ethernet-LAN), PC.
* Ein 3D-Drucker ist derzeit nicht erforderlich. Wenn du die 3D-Teile selbst drucken möchtest, werden M2- und M2,5-Schrauben und Muttern, die nicht in dieser Botkins-Teileliste aufgeführt sind, benötigt. Du findest sie in der upstream Vigibot-Teileliste in jedem der 3D-gedruckten Sektionen.
* Werkzeuge: Schraubenzieher, verstellbarer Schraubenschlüssel/Gabelschlüssel, Pinzette, Klebeband, ...

#### Geplante Verbesserungen am Leitfaden

Wir versuchen, den Bau der Botkins so einfach wie möglich zu gestalten, aber dieser Leitfaden ist nicht ganz so klar und einfach, wie wir es uns wünschen würden.
Verbesserungsvorschläge und Anregungen zu diesem Leitfaden sind sehr willkommen. Hilf uns, diesen Leitfaden durch Pull-Anfragen oder anderen Wegen zu verbessern.

#### Nächste Schritte (für Maker, die zur Verbesserung dieses Leitfadens beitragen möchten)

<details>
<summary>[Öffne diesen Abschnitt]</summary>
Bitte teile uns defekte Links oder Mängel (z. B. unklare oder fehlende Schritte) mit. 

* [x] Copy the parts from external guides into this guide and adjust accordingly for this specific build.
* [x] Translate the parts of the external guide from french to english.
* [ ] Move annotations and instructions that are littered through the partlist further down into the specific sections of the assembly guide. \[to be done by fire\_ned]
* [ ] extend the troubleshooting table
  * [ ] more scenarios
  * [ ] add pictures / gifs of led blinking patterns
  * [x] perhaps label whether that specific problem can happen during assembly (for makers) or during everyday use (for patients).
* [ ] add more function tests

</details>
</details>

## Teileliste

<details open>
<summary>[Diesen Abschnitt verbergen]</summary>
Zur einfacheren Lesbarkeit schlagen wir eine Bezugsquelle vor und listen Alternativen auf, wo vorhanden. Es ist euch selbstverständlich freigestellt, wo ihr die Teile beschafft.
Die meisten Teile können bei [robot-maker.com](https://www.robot-maker.com) beschafft werden

### Hauptteile

| Stk | Benennung | Shop | Alternative\* |
| --- | --- | --- | --- |
| 1 | Raspberry Pi 3B+ (or 3B), 1GB or 2GB | [Link](https://www.pi-shop.ch/raspberry-pi-3-model-b/) | [Alternative](https://www.robot-maker.com/shop/cartes-programmables/241-raspberry-pi-3b-plus-241.html) |
| 1 | Unlocked ZTE MF79 4G / LTE Stick | [Link](https://aliexpress.com/item/1005005844914823.html) | Huawei E3372h (Modell -153, -320 oder -607 |
| 1 | USB - USB 90° adapter | [Link, "Color : Down Angle Black"](https://aliexpress.com/item/1005003690522920.html) | - |
| 1 | USB bracket holder | [Link](https://www.robot-maker.com/shop/impression-3d/261-service-impression-3d-pla-261.html) | - |
| 1 | USB Microphone "Super AI". Die meisten anderen verfügbaren USB-Mikrofone sind leider entweder zu leise oder rauschen | [Link](https://www.robot-maker.com/shop/composants/446-microphone-usb-446.html) | [BOYA "Color : BY-M100UA"](https://aliexpress.com/item/1005004133896137.html) |
| 1 | 8-64GB "Endurance" Typ MicroSD Karte | [Link](https://www.robot-maker.com/shop/composants/91-carte-sd-32go-91.html) | [Alternative](https://www.berrybase.ch/sandisk-high-endurance-microsdhc-uhs-i-u3-speicherkarte-adapter-32gb) |
| 1 | Falls keinen vorhanden: CardReader für microSD | [Link](https://www.pi-shop.ch/sandisk-card-reader-usb-3-0-reader) | nach Belieben |
| 1 | Weitwinkelkamera mit Infrarot-Filter | [Link](https://www.robot-maker.com/shop/capteurs/311-camera-raspberry-pi.html) | [Alternative: "Color : Option 10"](https://aliexpress.com/item/1005004276506212.html) |
| 1 | 30cm Verbindungskabel für Kamera (zum ersetzen des kurzen Originals) | [Link](https://www.robot-maker.com/shop/composants/329-nappe-raspberry-pi.html#/92-longueur-30cm) | nach Belieben |
| 1 | Li-Ion Akku 1S2P 6800mAh | [Link](https://www.robot-maker.com/shop/alimentation/383-batterie-lithium-ion-1s2p-ncr-383.html) | Li-ion 1S2P 5-7Ah |
| 2 | 6A 67W Fast USB Charger | [Link, "Plug Type: EU Charger and Cable"](https://aliexpress.com/item/1005006632595521.html) | - |
| 1 | USB Kabel magnetisch | [Link, "Color : \*\* type c", "Length : 1m(3.3ft)"](https://www.aliexpress.com/item/4001224959039.html) | [Alternative Kabel](https://www.robot-maker.com/shop/alimentation/608-cable-usb-magnetique-data-608.html) + [Alternative Stecker "USB C"](https://www.robot-maker.com/shop/alimentation/609-embout-magnetique-micro-usb-ou-usb-c-rechargedata-609.html) |
| 1 | USB-A zu USB-C Kabel | [Link, "Color : A-C \*\* ", "Length : 1m"](https://aliexpress.com/item/1005008279278619.html) | nach Belieben |
| 1 | Active Buzzer 3V/5V, verbinde zwischen GND (kurzer Pin) und GPIO 18 | [Link, "activ"](https://www.robot-maker.com/shop/accessoires-robotiques/487-buzzer-5v-487.html) | [Alternative, "3v"](https://www.aliexpress.com/item/4000829554492.html) |
| 1 | Etwas Klett-Tape zum Befestigen der Batterie | [Link, "White 1Meter", "25mm Wide"](https://www.aliexpress.com/item/1005006680575466.html) | - |
| 1 | Falls noch keinen Vorhanden: Sekundenkleber | [Link, "1ML x10pcs"](https://aliexpress.com/item/1005008238433750.html) | - |
| 1 | Strommangement vigiUPSv2 | [Link](https://www.robot-maker.com/shop/alimentation/429-ups-hat-pour-raspberry-pi-429.html) | siehe "Hinweise zu Alternativen" |

Hinweis zum vigiUPSv2: Installiere die 2x Kamera-LEDs nicht, da sonst das Lademodul möglicherweise nicht mehr funktioniert, da der Akku aufgrund des zu hohen Leerlaufstromverbrauchs möglicherweise nie 100 % erreicht.

### \*Hinweise zu Alternativen:

Für gewisse Bauteile gibt es geprüfte Alternativen mit entsprechender Beschreibung.

<details>
<summary>[öffne diesen Abschnitt]</summary>

#### 4G / LTE Stick: Huawei E3372h

* Das neueste Modell "e3372h-325 (Brand: Brovi)" funktioniert nicht. Die älteren Modelle werden nicht mehr hergestellt.
* Finden Sie ein passendes Modell auf Secondhand-Plattformen. Das Modell muss „e3372h-153”, „e3372h-320” oder „e3372h-607” sein. Das Modell ist auf dem SIM-Steckplatz unter der Abdeckung aufgedruckt.
* Die funktionierenden e3372h-Modelle können zwei verschiedene Firmwares haben. (1) Die „hilink”-Firmware, die Plug\&Play-fähig ist und dem Pi eine IP-Adresse im Bereich 192.168.8.X zuweist. (2) Die „stick”-Firmware, die über ssh Verbindung via Terminal konfiguriert werden muss. [Anleitung](https://www.robot-maker.com/forum/topic/14850-how-to-use-the-e3372h-with-stick-firmware-instead-of-hilink-firmware/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) (Pi-Kenntnisse nötig)

#### UPS Alternativen

Seit Dezember 2025 wird das Geekworm UPS3 leider nicht mehr hergestellt.

* vigiUPSv3 sollte in einigen Monaten verfügbar sein. Bis dahin: Version aus der Teileliste (A) oder mit Mehraufwand (B)

Derzeit stehen folgende Alternativen zur Verfügung:

**A. vigiUPSv2**

Version aus der Teileliste, siehe oben

**B. Waveshare UPS hat (D)**

* <https://aliexpress.com/item/1005006100404260.html>

Funktioniert, benötigt jedoch einige Änderungen:

1_Ups_power

* Löte die Stromkabel für Servos und Motoren an den abgebildeten Stellen an.
* Gib einen Tropfen Sekundenkleber hinzu, um die Drähte auf der USV-Platine zu befestigen.
* Kaufe 2x 21700 Liion-Zellen anstelle des Akkus aus der Teileliste.
* Kaufe zusätzlich 4x 20 mm M2,5 Metall-Sechskantständer.
* Nimm 1x abgewinkelten USB-Stecker „toUp“ anstelle des „toDown“ aus der Teileliste.

Um die Spannungs- und Strommessungen zum Laufen zu bringen, verbinde dich per ssh mit dem Roboter und konfiguriere ihn:

B.1) Spannungsmessung:

3_Ups_sys_67

```
sudo nano /usr/local/vigiclient/sys.json
```

* Ändern in `"INA219ADDRESS": 67,`

B.2) Die Strommessung funktioniert auch, aber ich würde empfehlen, diesen Schritt zu überspringen, da er nicht so wichtig ist.

4_Ups_wrench5_Ups_I_conf\ 6_Ups_I_client

* Nimm die Änderungen wie in den Bildern gezeigt vor
* Da der Shunt-Widerstand 1/10 des üblicherweise verwendeten Widerstands beträgt und Vin+ und Vin- vertauscht sind, muss der Code in `/usr/local/vigibot/clientrobotpi.js` geringfügig geändert werden. Ich bin mir nicht sicher, ob das sinnvoll ist, da eine Änderung des Codes meines Wissens nach zukünftige automatische Vigibot-Updates deaktiviert.

Stromverteilung für den Waveshare UPS hat (D)

| Stk  | Benennung | Shop | Alternative |
| ---- | --- | --- | --- |
| 1 | Splitter Board | [Link, "Color : 1 pcs"](https://www.aliexpress.com/item/1005006042011391.html) | - |
| 1 | PH2.0 zu 2 Pin Kabel 10cm  | [Link, "Color : 2P", "Length : 10CM"](https://www.aliexpress.com/item/1005002901249753.html) | - |
</details>

### Basisplatte Motor

| Stk | Benennung | Shop | Alternative |
| --- | --- | --- | --- |
| 8-16 | DuPont-Kabel | [Link, "30cm" or "20cm"](https://www.robot-maker.com/shop/composants/42-nappe-40-fils-femelle-femelle-42.html) | [Alternative, "Color : Mix 10 Color", "Connector Type : Female to Female", "Pins : 30cm"](https://www.aliexpress.com/item/1005005365866477.html) |
| 5 | Einzelne DuPont Pin Hüllen | [Link, "1P"](https://aliexpress.com/item/33035707563.html) | - |
| 1 | Komplettes Kit mit Druckteilen, <br> Schrauben, Muttern und Distanzbolzen | [Link](https://www.robot-maker.com/shop/kits-robots/425-kit-chassis-4wd-minus-425.html) | - |
| 4 | Pololu 100:1 Getriebemotoren HP 6V <br> mit Kabeln zum selber löten | [Link](https://www.robot-maker.com/shop/moteurs-et-actionneurs/384-moteur-pololu-300-rpm.html) | [Alternative](https://www.pololu.com/product/1101) |
| 4 | Pololu Motorhalter Extended | [Link](https://www.robot-maker.com/shop/elements-mecaniques/385-support-moteur-pololu-long.html) | [Alternative](https://www.pololu.com/product/1089) |
| 4 | Pololu Räder 40x7mm <br> es gibt Radmodelle bei den 3D Daten <br> Durchmesser beachten kleiner 40mm | [Link](https://www.robot-maker.com/shop/elements-mecaniques/346-roue-pololu-40mm.html) | [Alternative](https://www.pololu.com/product/1454) |
| 1 | Feetech 2-Kanal Motortreiber <br> Kabel inkl. | [Link](https://www.robot-maker.com/shop/drivers-d-actionneurs/280-driver-convertisseur-moteur-cc-servomoteur.html) | - |

### Kopf-Teile

| Stk | Benennung | Shop | Alternative |
| --- | --- | --- | --- |
| 1 | Komplettes Kit mit Druckteilen, <br> Schrauben, Muttern und Distanzbolzen | [Link](https://www.robot-maker.com/shop/kits-robots/88-kit-tourelle-pan-tilt-88.html) | - |
| 1 + 1 Reserve | DM-S0090MD 180° oder 270° Metall Getriebe Servo 9g <br> (Kopf Schütteln) | [Link, "Color : 1PCS DM-S0090MD 180"](https://aliexpress.com/item/1005010339946695.html)  | [Alternative, "Color: 1PCS-270 Degree"](https://aliexpress.com/item/1005007890905728.html) |
| 1 + 1 Reserve | 180° Servo 9g <br> (Nicken) | [Link](https://www.robot-maker.com/shop/moteurs-et-actionneurs/18-servomoteur-9g-18.html) | |

Hinweis: Verwende die langen Schrauben, um die Servos auf dem Servohalter zu befestigen.

### Greifer-Teile

| Stk | Benennung | Shop |
| --- | --- | --- |
| 1 | Komplettes Kit mit Druckteilen, <br> Schrauben, Muttern und Distanzbolzen | [Link](https://www.robot-maker.com/shop/kits-robots/423-kit-pince-minus-423.html) |
| 2 | 180° Servo 9g | [Link](https://www.robot-maker.com/shop/moteurs-et-actionneurs/18-servomoteur-9g-18.html) |

Hinweis: Verwende die langen Schrauben, um die Servos auf dem Servohalter zu befestigen.

### Druckteile und Kleinteile, falls ihr selber druckt

In der Ordnerstruktur befinden sich die Druckteile in verschiedenen Formaten. Hier eine Auflistung der benötigten Teile in den jeweiligen Stückzahlen

<details>
<summary>[öffne diesen Abschnitt]</summary>

| Pos | Beschreibung | Benennung im Ordner | V2 | Bild |
| --- | --- | --- | :---: | :---: |
| 1 | Finger A zu Greifer | stl/clamp\_finger\_a.stl | 1 Stk | Finger A zu Greifer |
| 2 | Finger B zu Greifer | stl/clamp\_finger\_b.stl | 1 Stk | Finger B zu Greifer |
| 3 | Servoaufnahme Greifer | stl/clamp\_servo\_bracket.stl | 1 Stk | Servoaufnahme Greifer |
| 4 | Greiferhalter | stl/clamp\_u\_bracket.stl | 1 Stk | Greiferhalter |
| 5 | Servohalter Kopf schütteln | stl/head\_pan\_servo\_bracket.stl | 1 Stk | Servohalter Kopf schütteln |
| 6a  | Kopf ohne Smile | stl/head\_servo\_camera\_bracket\_nosmile.stl |  1 Stk <br> 6a oder 6b  | Kopf ohne Smile |
| 6b  | Kopf mit Smile | stl/head\_servo\_camera\_bracket\_smile.stl |  1 Stk <br> 6a oder 6b  | Kopf mit Smile  |
| 7 | Adapter Kopf schütteln | stl/head\_u\_bracket.stl | 1 Stk | Adapter Kopf schütteln |
| 8 | Motorhalter | stl/n20\_motor\_holder.stl | 4 Stk | Motorhalter |
| 9 | Bodenplatte | stl/plate\_bottom.stl | 1 Stk | Bodenplatte |
| 10  | Mittelplatte = <br> Motorplatte | stl/plate\_middle.stl | 1 Stk | Mittelplatte |
| 11a | Topplatte mit Lüfterloch | stl/plate\_top\_fan.stl | 1 Stk <br> 12a oder 12b | Topplatte Fan |
| 11b | Topplatte ohne Lüfterloch | stl/plate\_top\_nofan.stl | 1 Stk <br> 12a oder 12b | Topplatte No Fan |
| 12  | Rad 40 x 7mm | stl/pololu\_wheel\_40x7mm.stl | 4 Stk | Rad |
| 13  | Stosstange hinten | stl/rear\_protection.stl | 1 Stk | Stossstange |
| 14  | 4G Stick Halter | stl/usb\_bracket.stl | 1 Stk | 4G Stick Schutz |

### Kleinteile, falls ihr selber druckt

Anmerkung: Die Kamera <> Kopf Schrauben und Muttern müssen elektrisch leiten.

| Stk | Benennung | Dimmensionen  | wird verwendet für |
| --- | --- | --- | --- |
| 4 | Distanzbolzen M2.5 | Männchen 12mm | Pi <> UPS |
| 4 | Distanzbolzen M2.5 | Männchen 25mm | UPS <> Motorplatte |
| 4 | Distanzbolzen M2.5 | Weibchen 10mm | Grundplatte <> Motorplatte |
| 4 | Distanzbolzen M2.5 | Männchen 5mm  | Pi <> Topplatte |
| 10  | Schraube M2.5 | 6mm | 4x Topplatte <br> 4x Motorplatte <br> 2x Mittelplatte |
| 2 | Schraube M2.5 | 8 oder 10mm | für Motortreiber |
| 2 | Schraube M2.5 | 10 oder 12mm  | Pan Plate <> Roboter |
| 2 | Mutter M2.5 | - | 4x Motorplatte <br> 2x Mittelplatte <br> 2x Pan Plate |
| 4 | Schraube M2 | 20mm | 4x Kamera <> Kopf |
| 5 | Schraube M2 | 14 oder 16mm  | 2x 180° Servo <> Kopf <br> 5x Greifer |
| 1 | Schraube M2 | 10mm | 1x Greifer |
| 3 | Schraube M2 | 8mm | 3x Rückplatte <> Mittelplatte <br> 2x 270° Servo <> Pan Plate <br> 3x Greifer |
| 2 | Schraube M2 | 5 oder 6mm | ? |
| 15  | Mutter M2 | - | 3x Rückplatte <> Mittelplatte <br> 8x Kamera <br> 2x 270° Servo <> Pan Plate <br> 2x Greifer |

</details>
</details>

# Minus-Type Zusammenbau

<details open>
<summary>[Diesen Abschnitt verbergen]</summary>

## 1. Software Installieren

pi_cam<br>

Füge deinen Roboter bei Vigibot ganz einfach hinzu.
Du benötigst: einen Rapsery Pi (empfohlen 3B+), eine 16 oder 32 GB microSD Karte, eine Spannungsversorgung für den Pi, die Kamera mit dem passenden Kabel.
Mit wenigen einfachen Schritten kannst du deine Kamera auf [vigibot.com](https://www.vigibot.com/) live schalten:

* Erstelle auf [vigibot.com](https://www.vigibot.com/) einen Account.
* Klick auf "Management" und dann "Add a Robot". Wähle einen Namen für deinen Robter, den Roboter Typ Standard und ein Passwort für den Roboter. Das brauchen wir weiter unten gleich wieder, also merken.
* Lade das Image runter: [vigimage.zip](https://www.vigibot.com/vigimage/vigimage.zip) und entpacke die ZIP-Datei.
* Um die Image-Datei auf deine microSD Karte schreiben zu können, musst du diese mit dem PC verbinden (Kartenleser) und ein Tool zum Schreiben verwenden. Ich empfehle den Raspberry Pi Imager. Runterladen, installieren.
* Andere Tools wie das HDD Raw Copy Tool oder win32diskImager gehen auch. ApplePiBacker (Mac) oder balena etcher (Für Windows, Mac und Linux)
* Hinweis: Wenn du eine Karte grösser 32GB verwendest, musst du im Pi Imager zuerst das Modell 3 wählen, dann beim Betriebssystem löschen, um die Karte in FAT32 zu formatieren.
* Nach dem Ausführen des Pi Imager musst du das Modell des Pis auswählen, bei uns meist 3B+. Unter Betriebssystem wählst du zuunterst „Eigenes Image auswählen“, suchst das vigimage.img und wählst es aus. Dann wählst du die SD Karte als Zielmedium und bestätigst eine allfällige Überschreibewarnung. Starte den Schreibvorgang. Das dauert nun je nach Schreibgeschwindigkeit der Karte einige Minuten.
* Wenn das gemacht ist, öffne den /boot Ordner deiner SD Card. Windows: Sollte im Explorer der /boot Ordner nicht erscheinen, Drücke Win+R und gibt diskmgmt.msc ein. So gelangst du in die Datenträgerverwaltung. Wenn dort eine 100MB Partition gelistet ist, gib ihr über Rechtsklick > Laufwerkbuchstabe und -pfade ändern einen noch freien Buchstaben.
* Optional: Ändere die Datei "wpa\_supplicant.conf" mittels Rechtsklick und "in Editor anpassen" (Ändere die SSID „Demo“ und das Standardpasswort „Default“ entsprechend dem WLAN-Netzwerk, mit dem sich der Botkin verbinden soll. Tipp: Wenn (noch) kein 4G / LTE Stick vorhanden ist, kann mit dem Smartphone ein Hotspot eingerichtet werden. Vorteil: man kann den Botkin schon mitnehmen, wenn ein entsprechender Hotspot "mitreist". Nachteil: um auf den PI zuzugreifen via ssh, muss man im gleichen WLAN sein)
* Ändere die Datei "robot.json" gemäss dem zuvor gewählten Roboternamen und Roboterpasswort. ( Ändere den „Demo”-Benutzernamen und das „Standard”-Passwort)
* Installiere die SD-Karte im Raspberry Pi mit der installierten Kamera und schalte ihn dann ein (aufgrund des Kompilierungsprozesses dauert der erste Start einige Minuten, bevor der Roboter auf der Website erscheint (etwa 10 Minuten): Schalte den Raspberry Pi während dieser Zeit nicht aus).

Falls du auf den Pi zugreifen willst:
•	Der Pi und dein PC müssen in gleichen Netzwerk sein. Finde die IP Adresse des Pi raus (Verbindung über deinen Router (häufig hat der Router die IP 192.168.1.1) > Verbundene Geräte oder nutze eine App wie "Fing")
•	Win+R > „Powershell“ > Ausführen öffnet das Terminal
•	Gib im Fenster ein: ssh pi\@IP-ADRESSE (Ersetze die Adresse mit der Adresse des Pi, zB 192.168.1.146)
•	Das Terminal wird dich fragen, ob du sicher bist, eine Verbindung herstellen zu wollen. Schreibe „yes“ und bestätige
•	Verwende das Passwort, das du oben vergeben hast. Hast du robot.json nicht verändert, ist es „raspberry“.

* LTE/4G Mobile Data Stick:
* An einen Windows- oder Mac-PC anschliessen (die Webseite 192.168.8.1 wird geöffnet oder die App auf dem Speichermedium gestartet) und Datenroaming aktivieren.

## 2. Vigibot Online Konfiguration

#### Konfiguration der Fernsteuerung über Vigibot

Klicke auf der Vigibot Seite -> `Management` -> Werkzeug-Symbol (Remote controller configuration) -> `Modifications made` -> Wechsle von `Form` zu `Text` -> ersetze die `{}` mit dem folgenden Code:

<details>
<summary>[SHOW CODE BLOCK]</summary>

```JSON
{
  "BUTTONS": [
    {
      "ICON0": "vide",
      "ICON1": "",
      "TEXT": "",
      "ACTION": "",
      "SPECIAL": ""
    },
    {
      "ICON0": "vide",
      "ICON1": "",
      "TEXT": "",
      "ACTION": "",
      "SPECIAL": ""
    },
    {
      "ICON0": "vide",
      "ICON1": "",
      "TEXT": "",
      "ACTION": "",
      "SPECIAL": ""
    },
    {
      "ICON0": "avancer",
      "ICON1": "",
      "TEXT": "Forward",
      "ACTION": "IncrementForward",
      "SPECIAL": "yp"
    },
    {
      "ICON0": "vide",
      "ICON1": "",
      "TEXT": "",
      "ACTION": "",
      "SPECIAL": ""
    },
    {
      "ICON0": "suivant",
      "ICON1": "",
      "TEXT": "Next tool",
      "ACTION": "NextTool",
      "SPECIAL": ""
    },
    {
      "ICON0": "sirene0",
      "ICON1": "sirene1",
      "TEXT": "Buzzer",
      "ACTION": "Switch2",
      "SPECIAL": "i2"
    },
    {
      "ICON0": "lumicont0",
      "ICON1": "lumicont1",
      "TEXT": "Maximize the brightness and contrast",
      "ACTION": "Switch3",
      "SPECIAL": "i3"
    },
    {
      "ICON0": "gauche",
      "ICON1": "",
      "TEXT": "Left",
      "ACTION": "IncrementTurnLeft",
      "SPECIAL": "zn"
    },
    {
      "ICON0": "stopper",
      "ICON1": "",
      "TEXT": "Click to stop or drag to drive",
      "ACTION": "Brake",
      "SPECIAL": "st"
    },
    {
      "ICON0": "droite",
      "ICON1": "",
      "TEXT": "Right",
      "ACTION": "IncrementTurnRight",
      "SPECIAL": "zp"
    },
    {
      "ICON0": "centrer",
      "ICON1": "",
      "TEXT": "Reset tools",
      "ACTION": "ResetTools",
      "SPECIAL": ""
    },
    {
      "ICON0": "vide",
      "ICON1": "",
      "TEXT": "",
      "ACTION": "",
      "SPECIAL": ""
    },
    {
      "ICON0": "vide",
      "ICON1": "",
      "TEXT": "",
      "ACTION": "",
      "SPECIAL": ""
    },
    {
      "ICON0": "vide",
      "ICON1": "",
      "TEXT": "",
      "ACTION": "",
      "SPECIAL": ""
    },
    {
      "ICON0": "reculer",
      "ICON1": "",
      "TEXT": "Backward",
      "ACTION": "IncrementBackward",
      "SPECIAL": "yn"
    },
    {
      "ICON0": "capture",
      "ICON1": "",
      "TEXT": "Capture the last seconds of video",
      "ACTION": "",
      "SPECIAL": "capture"
    },
    {
      "ICON0": "precedent",
      "ICON1": "",
      "TEXT": "Previous tool",
      "ACTION": "PreviousTool",
      "SPECIAL": ""
    },
    {
      "ICON0": "vide",
      "ICON1": "",
      "TEXT": "",
      "ACTION": "",
      "SPECIAL": ""
    },
    {
      "ICON0": "vide",
      "ICON1": "",
      "TEXT": "",
      "ACTION": "",
      "SPECIAL": ""
    },
    {
      "ICON0": "lock0",
      "ICON1": "lock1",
      "TEXT": "Unlink remote control and video",
      "ACTION": "",
      "SPECIAL": "switchlock"
    },
    {
      "ICON0": "osd0",
      "ICON1": "osd1",
      "TEXT": "Toggle OSD",
      "ACTION": "",
      "SPECIAL": "switchosd"
    },
    {
      "ICON0": "vide",
      "ICON1": "",
      "TEXT": "",
      "ACTION": "",
      "SPECIAL": ""
    },
    {
      "ICON0": "dodo",
      "ICON1": "",
      "TEXT": "Put on standby",
      "ACTION": "Sleep",
      "SPECIAL": ""
    },
    {
      "ICON0": "vide",
      "ICON1": "",
      "TEXT": "",
      "ACTION": "",
      "SPECIAL": ""
    },
    {
      "ICON0": "vide",
      "ICON1": "",
      "TEXT": "",
      "ACTION": "",
      "SPECIAL": ""
    },
    {
      "ICON0": "vide",
      "ICON1": "",
      "TEXT": "",
      "ACTION": "",
      "SPECIAL": ""
    },
    {
      "ICON0": "exit",
      "ICON1": "",
      "TEXT": "Restart the client process",
      "ACTION": "ExitRobot",
      "SPECIAL": "confirm"
    },
    {
      "ICON0": "reboot",
      "ICON1": "",
      "TEXT": "Reboot the system",
      "ACTION": "RebootRobot",
      "SPECIAL": "confirm"
    },
    {
      "ICON0": "poweroff",
      "ICON1": "",
      "TEXT": "Power off the system",
      "ACTION": "PowerOffRobot",
      "SPECIAL": "confirm"
    }
  ],
  "COMMANDS": [
    {
      "NAME": "Camera control",
      "CAMERA": 0,
      "MIXING": 0,
      "GAINX": 80,
      "GAINY": 80
    },
    {
      "NAME": "Gripper control",
      "CAMERA": 0,
      "MIXING": 1,
      "GAINX": 80,
      "GAINY": 80
    },
    {
      "NAME": "250 Kbps - Camera control",
      "CAMERA": 1,
      "MIXING": 0,
      "GAINX": 80,
      "GAINY": 80
    },
    {
      "NAME": "250 Kbps - Gripper control",
      "CAMERA": 1,
      "MIXING": 1,
      "GAINX": 80,
      "GAINY": 80
    }
  ],
  "TX": {
    "COMMANDS16": [
      {
        "NAME": "Turret X",
        "INIT": 0,
        "SCALEMIN": -180,
        "SCALEMAX": 180,
        "MIN": -90,
        "MAX": 90,
        "CLAMPMIN": -20,
        "CLAMPMAX": 20,
        "SIGNED": true,
        "NBDIGITS": 2,
        "UNIT": "°"
      },
      {
        "NAME": "Turret Y",
        "INIT": 0,
        "SCALEMIN": -180,
        "SCALEMAX": 180,
        "MIN": -55,
        "MAX": 55,
        "CLAMPMIN": -40,
        "CLAMPMAX": 20,
        "SIGNED": true,
        "NBDIGITS": 2,
        "UNIT": "°"
      },
      {
        "NAME": "Gripper X",
        "INIT": 0,
        "SCALEMIN": -180,
        "SCALEMAX": 180,
        "MIN": -30,
        "MAX": 65,
        "CLAMPMIN": -20,
        "CLAMPMAX": 65,
        "SIGNED": true,
        "NBDIGITS": 2,
        "UNIT": "°"
      },
      {
        "NAME": "Gripper Y",
        "INIT": 0,
        "SCALEMIN": -180,
        "SCALEMAX": 180,
        "MIN": -40,
        "MAX": 80,
        "CLAMPMIN": 0,
        "CLAMPMAX": 45,
        "SIGNED": true,
        "NBDIGITS": 2,
        "UNIT": "°"
      }
    ]
  }
}
```

</details>
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

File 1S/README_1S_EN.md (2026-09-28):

# Minus-Type 1S Vigibot Robot for Botkins
<details open>
<summary>[HIDE SECTION]</summary>

### Table of Contents
- [General Info](#general-info)
- [Prerequisites](#prerequisites)
- [Partlist](#partlist)
  - [Core Parts](#core-parts)
  - [UPS Alternatives](#ups-alternatives)
  - [Power Distribution Board Parts](#power-distribution-board-parts)
  - [Motor Base Parts](#motor-base-parts)
  - [Head Parts](#head-parts)
  - [Gripper Parts](#gripper-parts)
  - [Optional Parts](#optional-parts)
- [Minus-Type Assembly](#minus-type-assembly)  
    - [1. Software Install](#1-software-install)  
    - [2. Vigibot Online Configuration](#2-vigibot-online-configuration)  
    - [3. UPS Solder Bridge](#3-ups-solder-bridge)  
    - [4. Servo Plug Split](#4-servo-plug-split)  
    - [5. Power Distribution Assembly](#5-power-distribution-assembly)  
    - [6. GPIO Wiring](#6-gpio-wiring)  
    - [7. Motor Base Assembly](#7-motor-base-assembly)  
    - [8. Head Assembly](#8-head-assembly)  
    - [9. Gripper Assembly](#9-gripper-assembly)  
    - [10. Final Assembly](#10-final-assembly)  
    - [11. Optional Assemblies](#11-optional-assemblies)  
    - [12. Additional Assembly Guides](#12-additional-assembly-guides)
    - [13. Function Tests](#13-function-tests)
- [Troubleshooting](#troubleshooting)
- [Credits](#credits)

### General Info
Learn more about Botkins Charity Project:
- [botkins.ch (German)](https://botkins.ch)
- [Hackaday Page](https://hackaday.io/project/180558-botkins-charity-project)  

Learn more about Vigibot:
- [Robot Maker Post](https://www.robot-maker.com/forum/topic/13010-what-is-vigibot-quest-ce-que-vigibot/)
- [Drive a robot Vigibot.com](https://www.vigibot.com/)

Basis is the Standard Vigibot Minus-Type (pictured), but with a LTE/4G stick and without lateral (side) arms

Standard Minus

- If you'd like to build a robot for Botkins, contact us and we'll send you the Onboarding Process. 
- The maker can choose the 3D printed parts color.
- Building your first robot may take about 10 hours, maybe more. After some practice, building may take about 3h per robot.
- Some parts from aliexpress may take 5 weeks to arrive. currently (2025) setting payment method to paypal will fail with "Sorry, some items are not available", credit card works. Disable [E-Mail order updates](https://www.aliexpress.com/p/edm-setting/index.html) before checking out, else you'll get 3-5 E-Mails per item.
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

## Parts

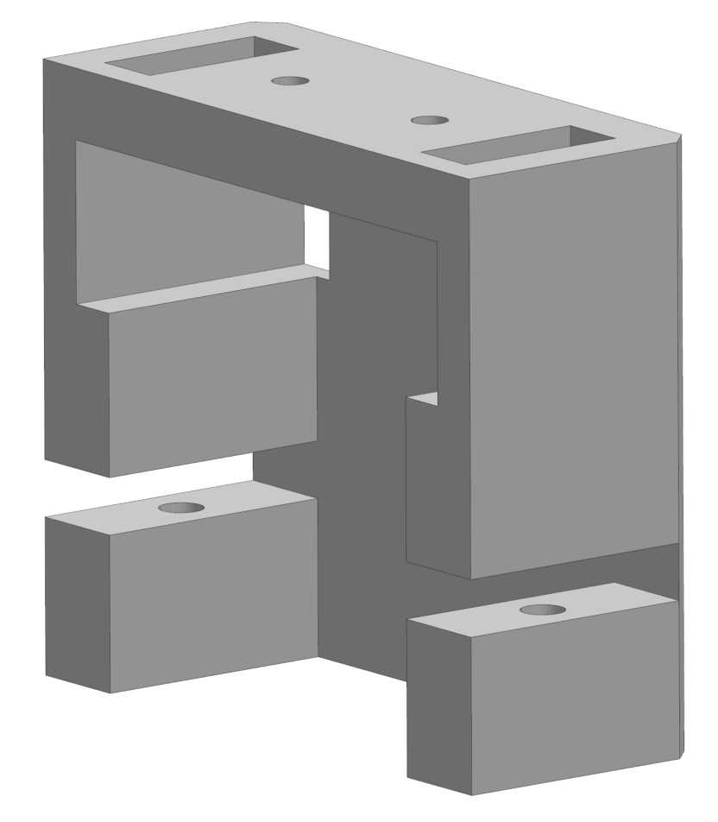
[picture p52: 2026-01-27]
images/3D-parts/generic_servo_bracket.jpg

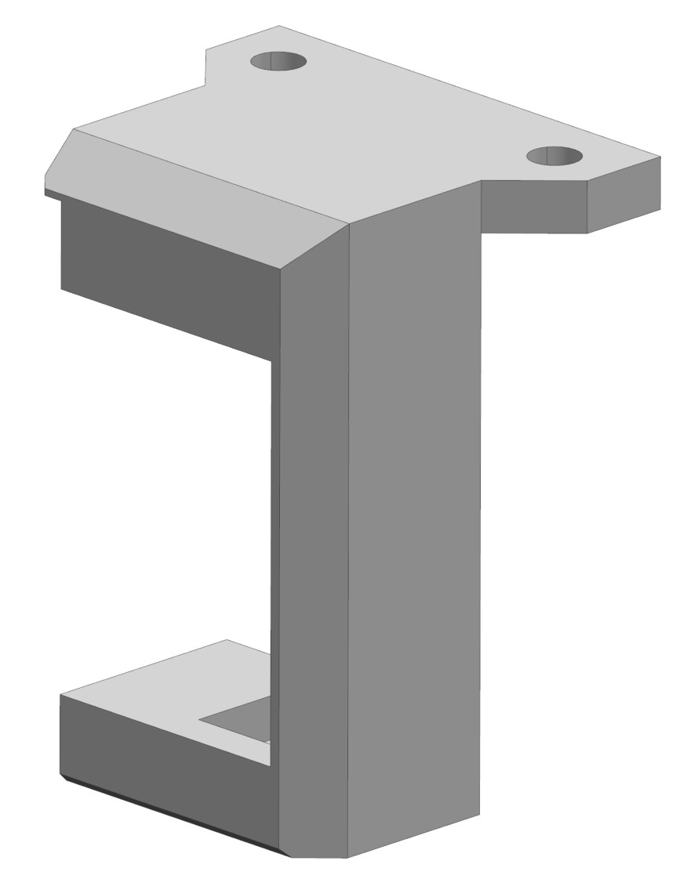
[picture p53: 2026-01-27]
images/3D-parts/get_up_servo_bracket_a.jpg

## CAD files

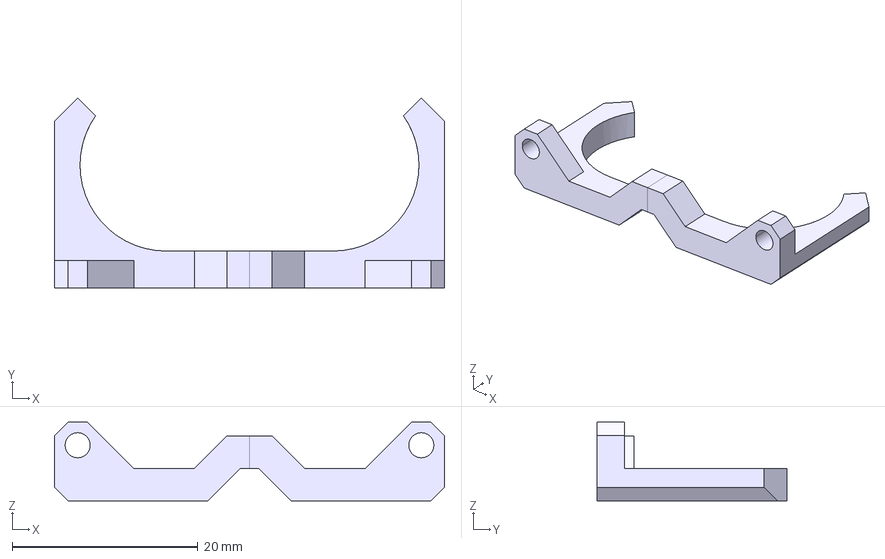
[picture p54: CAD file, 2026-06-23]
2S/3D_files/Chassis/2S102.0 Batteriehalter.step
42.0 x 20.5 x 8.50 mm

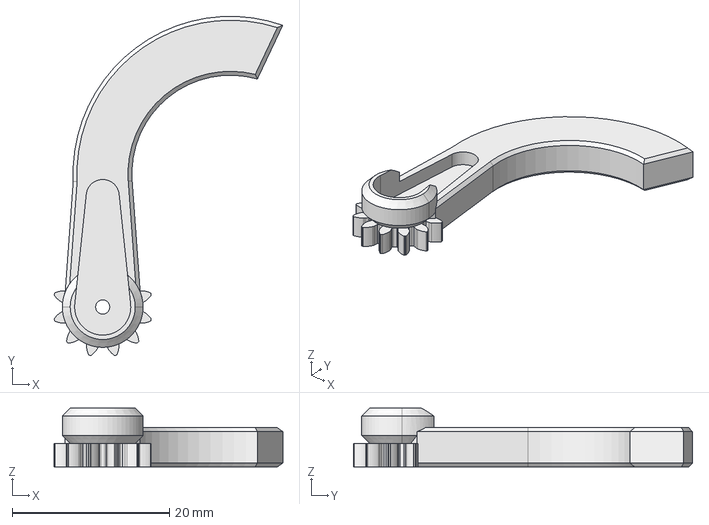
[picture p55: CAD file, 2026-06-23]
2S/3D_files/Greifer/2S105.0 Greifer Finger Links.step
29.1 x 43.1 x 7.50 mm

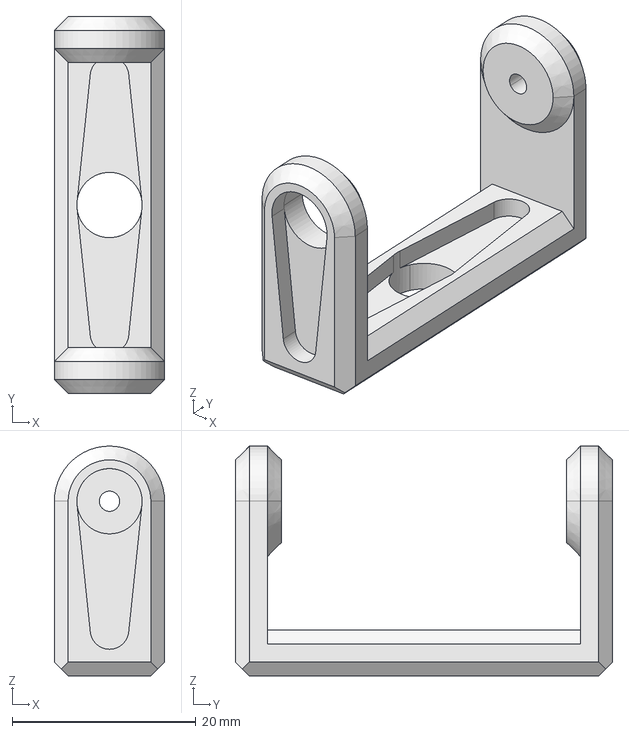
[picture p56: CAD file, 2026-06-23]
2S/3D_files/Kopf/2S107.0 Kopfhalter.step
12.0 x 41.0 x 25.0 mm

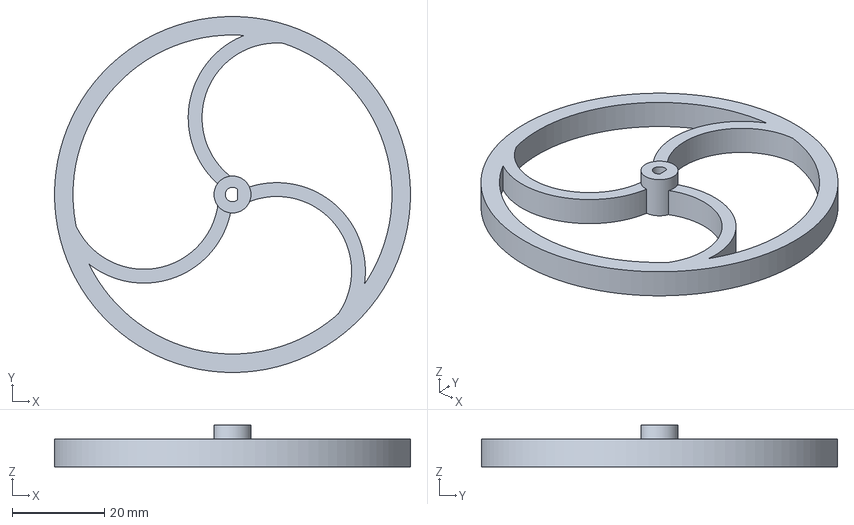
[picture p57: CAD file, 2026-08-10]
cad/3mf/HighlyConfigurableWheelv1.32_Pascal_rev.3mf
77.0 x 77.0 x 9.00 mm

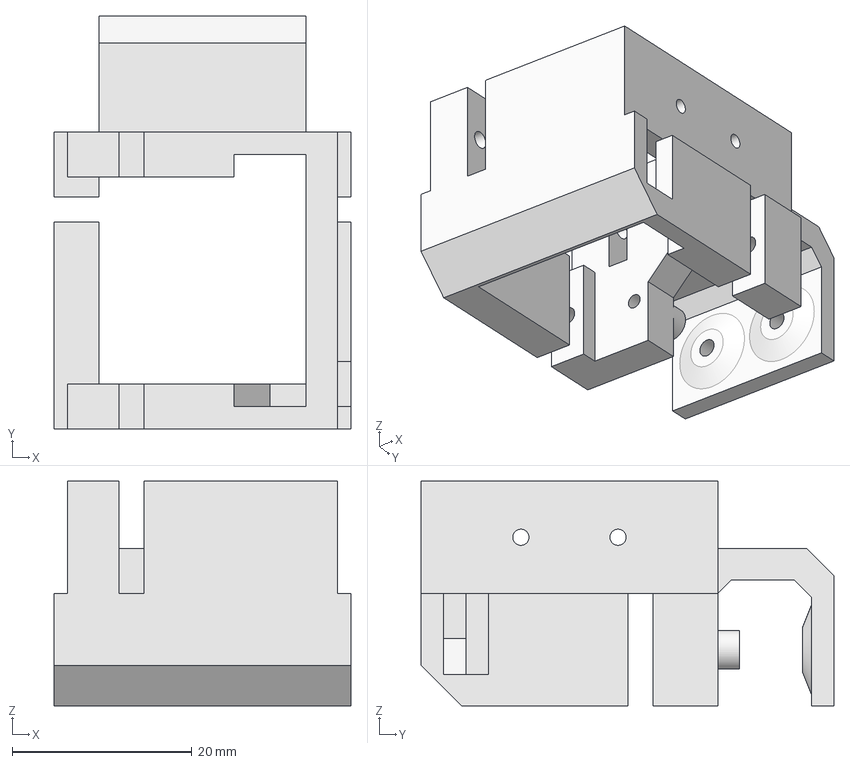
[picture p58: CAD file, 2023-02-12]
cad/modifications_botkins/clamp_servo_bracket_botkins_V31.3mf
33.0 x 45.9 x 25.0 mm

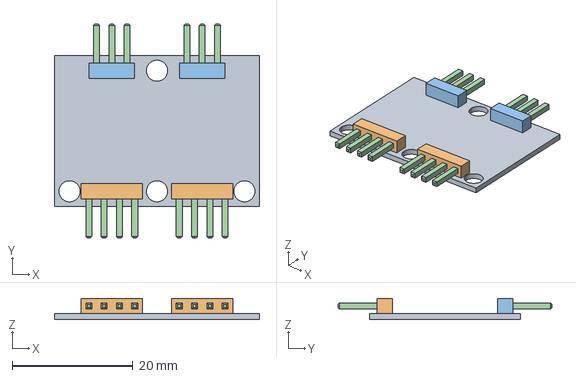
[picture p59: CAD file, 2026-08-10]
cad/step/feetech_2ch_board.step
34.0 x 35.5 x 3.50 mm

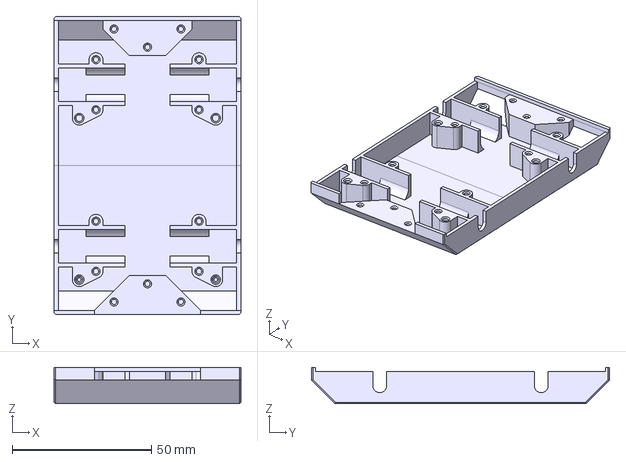
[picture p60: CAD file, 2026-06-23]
2S/3D_files/Chassis/2S101.0 Basis.step
67.0 x 107.0 x 13.1 mm

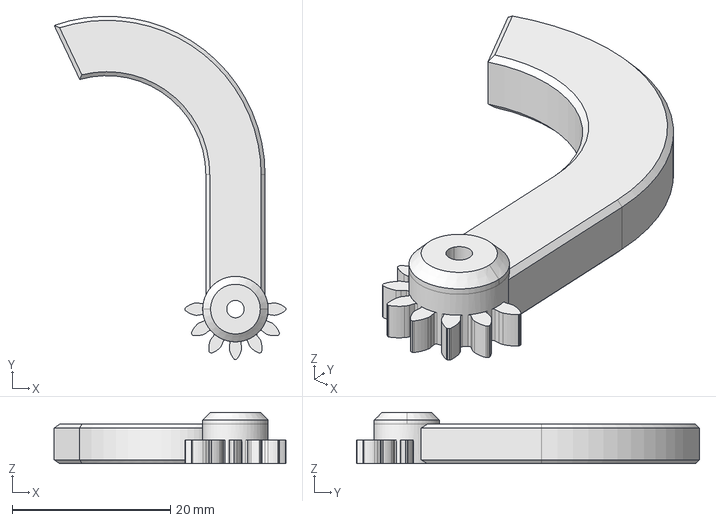
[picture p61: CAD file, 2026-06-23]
2S/3D_files/Greifer/2S106.0 Greifer Finger Rechts.step
29.3 x 43.3 x 6.50 mm

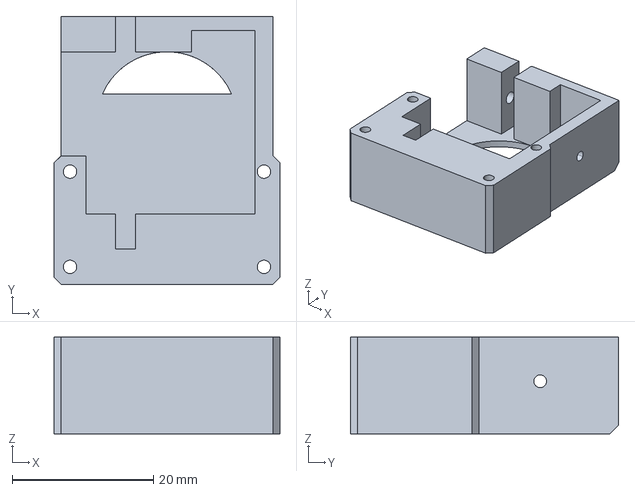
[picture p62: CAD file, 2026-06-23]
2S/3D_files/Kopf/2S108.0 Smilie Kopf und Kamerahalter.step
32.0 x 38.0 x 13.7 mm

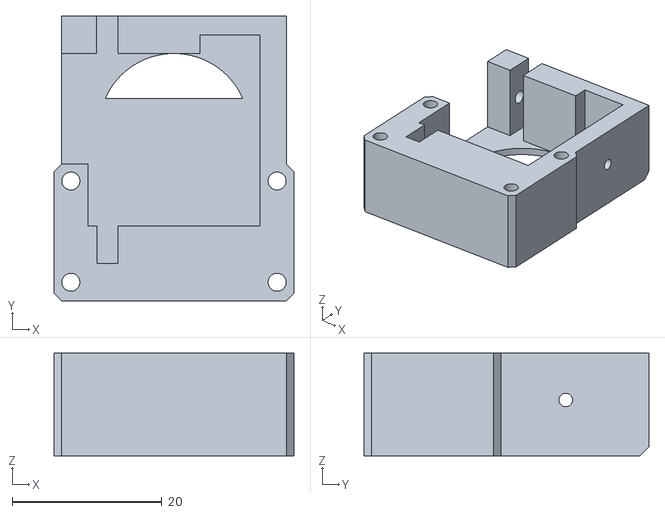
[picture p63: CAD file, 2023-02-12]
cad/modifications_botkins/head_servo_camera_bracket_smile_botkins.stl
32.0 x 38.0 x 13.7

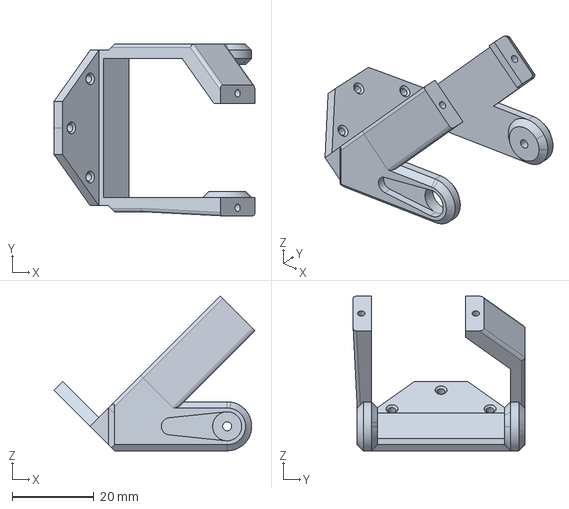
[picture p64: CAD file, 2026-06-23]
2S/3D_files/Greifer/2S103.0 Kopf und Greiferhalter.step
49.1 x 42.0 x 37.8 mm

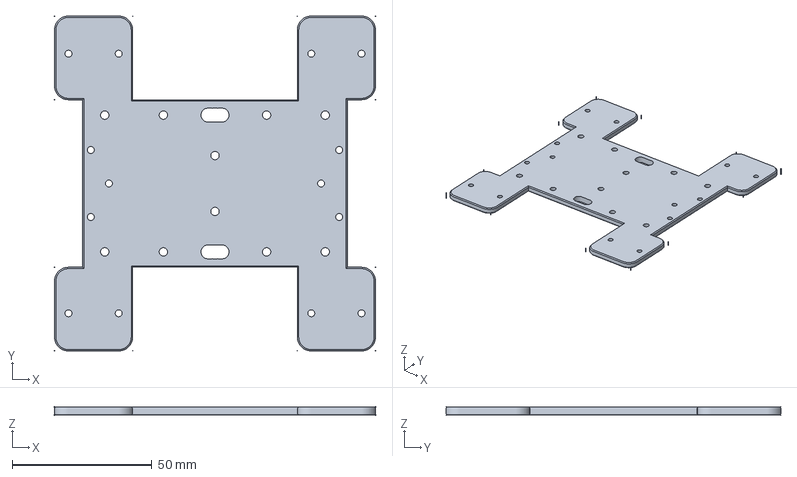
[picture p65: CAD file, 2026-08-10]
cad/3mf/plate_middle_big_wheels.3mf
115.0 x 120.0 x 3.00 mm

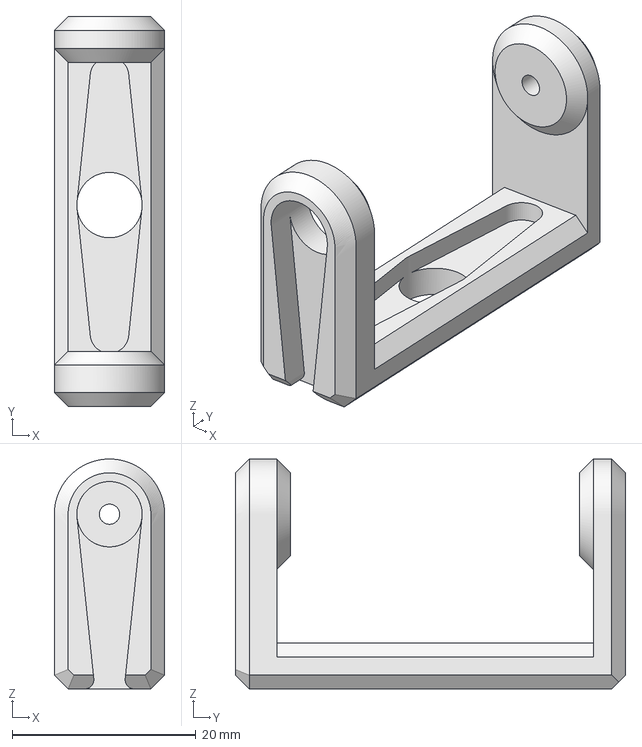
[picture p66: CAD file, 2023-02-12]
cad/modifications_botkins/head_u_bracket_botkins_V2.3mf
12.0 x 42.4 x 25.0 mm

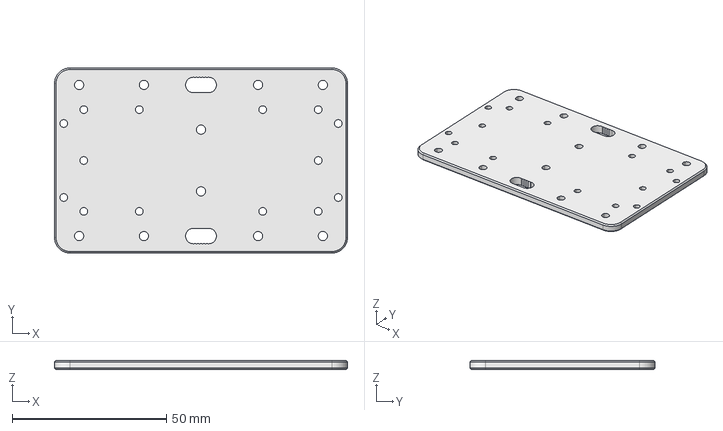
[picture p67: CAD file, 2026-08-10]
cad/step/plate_middle.step
95.0 x 60.0 x 3.00 mm

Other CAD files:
cad/3mf/HighlyConfigurableWheelv1.32_Pascal.3mf
cad/step/head_servo_camera_bracket_smile.step
cad/3mf/rear_protection_long.3mf
cad/modifications_botkins/clamp_u_bracket_botkins_V3.3mf
cad/scad/printable/HighlyConfigurableWheelv1.32_Pascal.scad
cad/scad/printable/Highly_Configurable_Wheel_One_Wheel_To_Rule_Them_All/HighlyConfigurableWheelv1.32.scad
cad/scad/printable/Highly_Configurable_Wheel_One_Wheel_To_Rule_Them_All/HighlyConfigurableWheelv1.33.scad
cad/scad/printable/clamp_servo_bracket.scad
cad/3mf/clamp_finger_a.3mf
cad/3mf/clamp_finger_b.3mf
cad/3mf/clamp_servo_bracket.3mf
cad/3mf/clamp_u_bracket.3mf
cad/3mf/generic_servo_bracket.3mf
cad/3mf/get_up_servo_bracket_a.3mf
cad/3mf/get_up_servo_bracket_b.3mf
cad/3mf/head_pan_servo_bracket.3mf
cad/3mf/head_servo_camera_bracket_nosmile.3mf
cad/3mf/head_servo_camera_bracket_smile.3mf
cad/3mf/head_u_bracket.3mf
cad/3mf/photoresistor_cap.3mf
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

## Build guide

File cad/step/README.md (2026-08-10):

# Make your own Vigibot.com raspberry PI robot

## Raspberry PI robot STEP CAD files

### Note

- All source files are available in openscad format. 
- Source files are made with parameters for easy modification. 
- If you want make a modification it's better to make them in openscad in order to ba able to share your modified source file. 
- The OpenSCAD software available at https://www.openscad.org to open or customize SCAD files

### All pieces needed for the standard Vigibot

Liste of all Minus 3D files in step format
If you use them and make modifications, share your update. 

You can discuss about 3D model in our discord : https://discord.gg/3KrMHdp
or on the forum : https://www.robot-maker.com/forum/213-vigibot/

#### Todo

- Add non 3D printed files like wheels camera, servomotors ... 
- Make a full 3D model assembly ...

#### Done

##### All 3D printed files

- clamp_finger_a.step
- clamp_finger_b.step
- clamp_servo_bracket.step
- clamp_u_bracket.step
- generic_servo_bracket.step
- get_up_servo_bracket_a.step
- get_up_servo_bracket_b.step
- head_pan_servo_bracket.step
- head_servo_camera_bracket_nosmile.step
- head_servo_camera_bracket_smile.step
- head_u_bracket.step
- photoresistor_cap.step
- plate_bottom.step
- plate_middle.step
- plate_middle_big_wheels.step
- plate_top_fan.step
- plate_top_nofan.step
- rear_protection.step
- rear_protection_long.step
- servo_finger_a.step
- servo_finger_b.step
- usb_bracket.step

##### All standard parts 

- n20_motor_holder.step

##### Custom parts

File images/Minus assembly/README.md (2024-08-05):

# Minus Assembly Images

## Camera Assembly
Camera assembly-1
Camera assembly-2

## Final Assembly
Final assembly-1
Final assembly-2
Final assembly-3
Final assembly-4
Final assembly-5
Final assembly-6
Final assembly-7
Final assembly-8
Final assembly-9

## Gripper Assembly
Gripper assembly-1
Gripper assembly-2
Gripper assembly-3
Gripper assembly-4
Gripper assembly-5
Gripper assembly-6
Gripper assembly-7

## Middle Plate Assembly
Middle plate assembly-1
Middle plate assembly-2
Middle plate assembly-3
Middle plate assembly-4
Middle plate assembly-5
Middle plate assembly-6
Middle plate assembly-7
Middle plate assembly-8
Middle plate assembly-9
Middle plate assembly-10

## Pan & Tilt Turret Assembly
Pan + Tilt turret assembly-1
Pan + Tilt turret assembly-2

## Pan Turret Assembly
Pan turret assembly-1
Pan turret assembly-2

## Side Arm Assembly
Side Arm A assembly-1
Side Arm A assembly-2
Side Arm B assembly

## Tilt Turret Assembly
Tilt turret assembly-1
Tilt turret assembly-2

## Top Plate Assembly
Top plate assembly-1
Top plate assembly-2

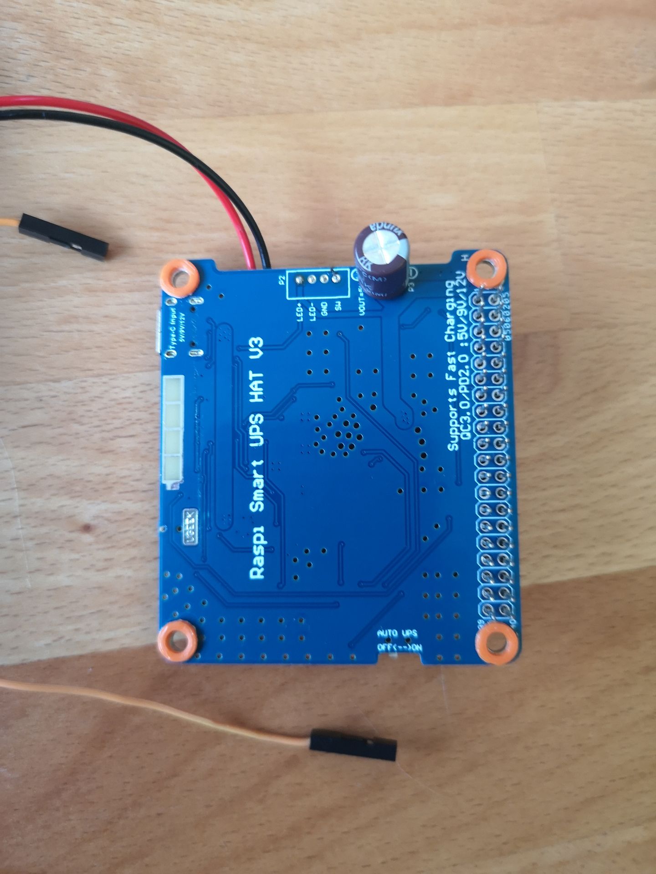
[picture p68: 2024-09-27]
images/Minus_assembly_Botkins/wiring_assembly_2.jpg

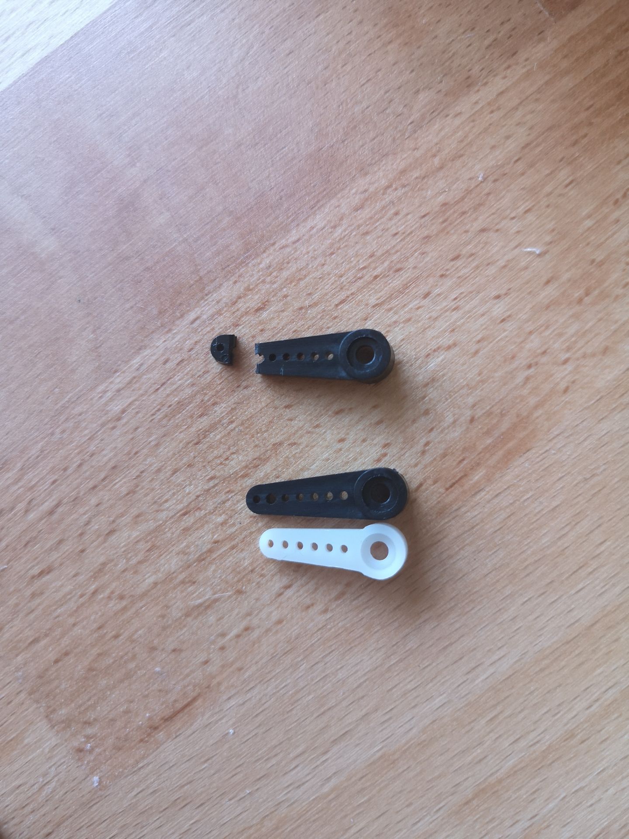
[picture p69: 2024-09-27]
images/Minus_assembly_Botkins/metal_servo_horn_1.jpg

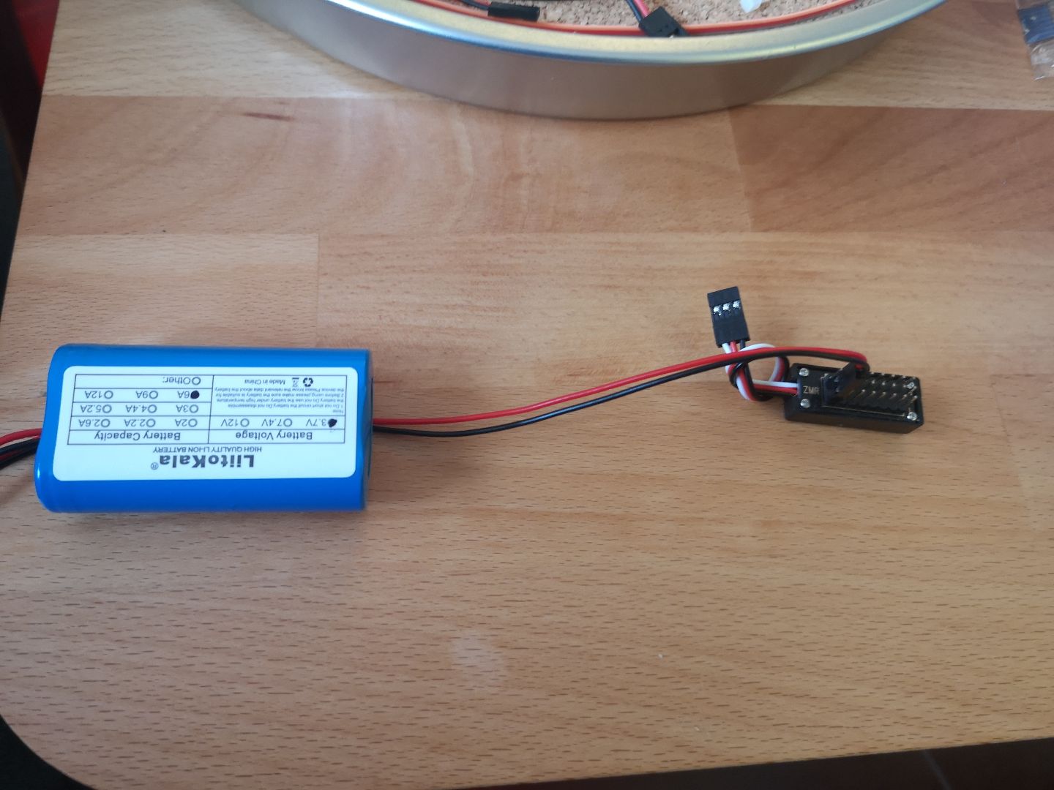
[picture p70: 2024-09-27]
images/Minus_assembly_Botkins/pdb_assembly_2.jpg

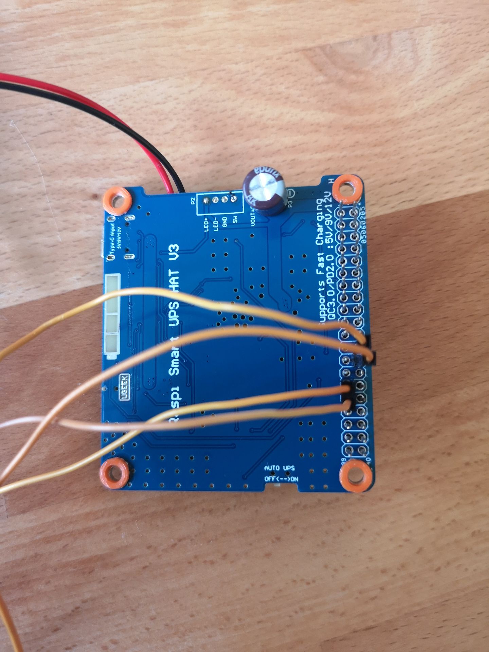
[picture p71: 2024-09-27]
images/Minus_assembly_Botkins/wiring_assembly_4.jpg

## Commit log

2022-08-10 3D parts list, gripper missing
2022-08-10 updated 3d print list with filenames
2022-08-11 printer required
2022-08-13 rm wrong driver
2022-08-15 working on standoffs
2022-08-15 nuts screws usb bracket
2022-08-15 core screws done
2022-08-17 working on head and gripper screws
2022-08-17 added motor mount screws
2022-08-17 set mm for head, u-bracket
2022-08-17 added flathead for motor drv
2022-08-17 power distribution board
2022-08-17 rm back plate
2022-08-18 m2.5 screw for metal gear servo
2022-08-18 clamp finger
2022-08-19 rm photo resistor cap
2022-08-19 white led
2022-08-19 12mm Heatshrink
2022-08-19 6 pd board
2022-08-22 led lens caps
2022-08-27 2x magnetic
2022-10-17 m2 conductive screw, m2 spacer
2022-10-17 spacers replace middle nuts
2022-10-17 usb charger 3A
2022-10-17 motor bracket screws, nuts
2022-10-17 conductive nut
2022-10-22 no fitec servo
2022-10-23 magnetic cable
2022-11-14 4x2 spacers cam
2022-11-19 25mm head screws
2023-01-02 thanks Narayan for this mod
    [plate_bottom_sidewalls.stl]
2023-02-12 DIYMore MG90S 3D files
    modified by Maker Caiman
    [clamp_finger_a_botkins.stl, clamp_servo_bracket_botkins_V31.3mf, clamp_u_bracket_botkins_V3.3mf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]
2023-02-12 with sidewalls
    modified by Narayan
    [plate_bottom_sidewalls.stl]
2023-02-12 mv sidewalls
    [plate_bottom_sidewalls.stl]
2023-08-14 rm 7mm heat shrink
2023-09-03 20mm screws
2023-09-10 17mm standoff + hex->philips screws
2023-09-10 2x1, 2x2, etc spacers
2023-09-10 pd board rephrase
2024-02-03 Backup metal gear partlist 2023
2024-06-10 motor parts synced
2024-08-04 usb bracket holder
2024-08-05 assembly sort
2024-08-05 assembly in main readme
2024-08-14 mag 4 pin
2024-09-27 assembly images upload
2024-09-27 insert pictures
2024-09-29 assembly guide links now
2024-10-13 motor base guide
2024-10-16 motor FR
2024-10-31 solder help
2024-12-25 hq ali dupont cables 2
2024-12-30 power upa not pi
2024-12-30 motor split
2025-05-26 battery resistance
2025-08-06 with cable
2025-10-04 rm pdb battery
2025-10-04 bat solder2
2025-12-25 1m cable2
2026-01-11 rm de. links
2026-01-19 Create README_DE.md
    German Version for the Swiss Makers - under construction
    Deutsche Version für die Schweizer Makers - in Bearbeitung
2026-01-24 Update README_DE.md
    Stand 24.01.26
    Versuch Darstellung Bilder 3D Druckteile in Tabelle
    Wird mit besseren Renderings fortgeführt
2026-03-21 250kbps gripper
2026-04-17 new usb charger
